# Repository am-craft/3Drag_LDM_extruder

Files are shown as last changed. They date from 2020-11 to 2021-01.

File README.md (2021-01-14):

# 3Drag LDM extruder

This repository contain all the 3D model designed for the 3Drag 3D printer's extruder @ [+LAB](www.piulab.it).






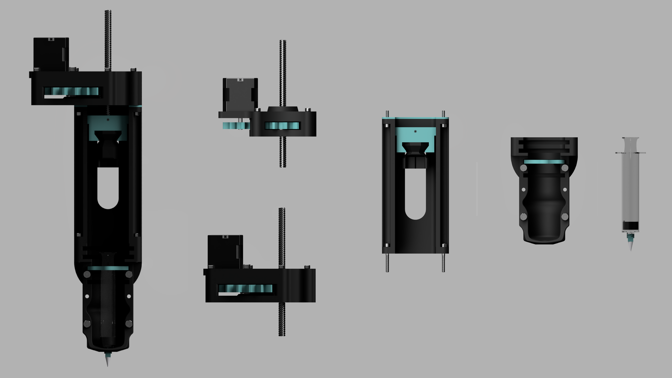
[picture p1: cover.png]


LDM (liquid Deposition Modeling) is a particular 3D printer process in which viscous fluid are extruded from a reservoir and deposited on the build plate. This process is also known as Direct Ink Writing (DIW).

The third version of the LDM extruder was developed with the porpuse of making a modular extruder, easy to assemble and disasseble.
- The syringe holder is stronger of the previour version and can be used to easily mount syringe from 10ml to 60ml.
- The extruder assembly is divided into three main parts. If one component broke you can easily switch is without disassembling all the extruder.
- The completely redesigned drive unit is stronger and smoother. The M8 screw has been substituted with a T8 lead screw. Two version are available with a 2:1 and 4:1 reduction. Higher reduction provide higher extrusion force and higher precision over the extruded material volume.
### Firmware mods needed:
- Change _DEFAULT_AXIS_STEPS_PER_UNIT_ for E motor according to the following equation: 
- Set to dummy the E0 thermistor.
- Set to 20°C the minimum temperature for preventing extrusion.

[BOM](https://github.com/am-craft/3Drag_LDM_extruder/blob/main/BOM.md)

Previous version of the extruder are available at thingiverse: [version 1](https://www.thingiverse.com/thing:482873), [version 2](https://www.thingiverse.com/thing:4635819)

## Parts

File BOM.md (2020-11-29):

# BOM

### Mount plate

* 4x nut M5

### Syringe holder:

* 4x bolt M5x50
* 4x nut M4

### Guide

* 2x square nut M3
* 2x set screw M3x10
* 1x bolt M4x10
* 4x bolt M4x16
* 4x bolt M4x30
* 2x steel rod (or tube) 4x157

### Gearbox 2:1 reduction

* 4x bolt M4x30
* 8x nut M4
* 2x trust bearing 10x24x9 [amazon](https://www.amazon.it/gp/product/B07G7YQS48/ref=ppx_yo_dt_b_asin_title_o02_s00?ie=UTF8&psc=1&tag=tv-auto-20)
* 1x T8 lead screw 8x200 [amazon](https://www.amazon.it/SIENOC-piombo-stampante-motore-passo-passo/dp/B07LDZY8RY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)
* 4x flat-head bolt M3x12
* 4x set screw M4x8
* 1x Nema 17 stepper motor

### Gearbox 4:1 reduction

* 5x bolt M4x40
* 10x nut M4
* 1x bolt M5x40
* 1x nut M5
* 2x trust bearing 10x24x9 [amazon](https://www.amazon.it/gp/product/B07G7YQS48/ref=ppx_yo_dt_b_asin_title_o02_s00?ie=UTF8&psc=1&tag=tv-auto-20)
* 2x trust bearing 8x16x5 [amazon](https://www.amazon.it/gp/product/B075F76KHN/ref=ppx_yo_dt_b_asin_title_o00_s00?ie=UTF8&psc=1)
* 1x T8 lead screw 8x200 [amazon](https://www.amazon.it/SIENOC-piombo-stampante-motore-passo-passo/dp/B07LDZY8RY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)
* 4x flat-head bolt M3x12
* 4x set screw M4x8
* 1x Nema 17 stepper motor

### Tools

* M4 tapper
* 8mm drill bit
* saw
* screwdrivers
* hex keys

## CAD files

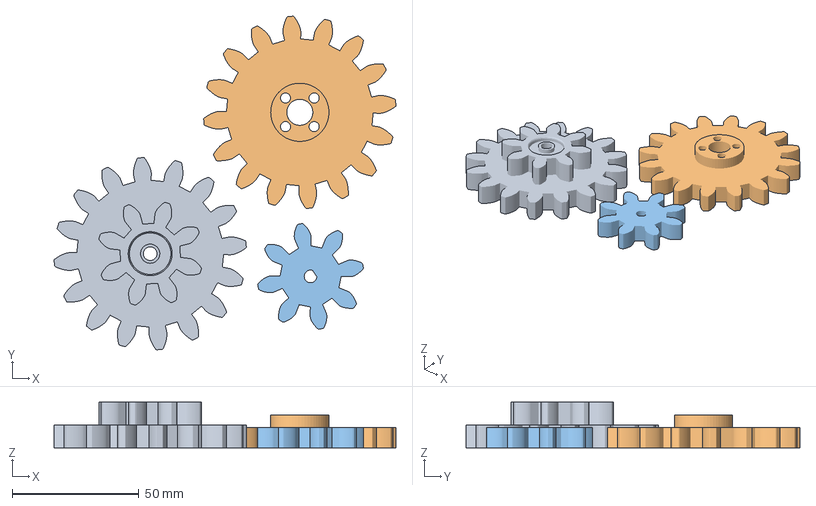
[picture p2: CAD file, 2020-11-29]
print files/4r_gears_v3.2.0.3mf
135.2 x 131.9 x 18.0 mm
4r_middle gear_v3.2.0.stl
4r_screw gear_v3.2.0.stl
motor gear_v3.0.0.stl

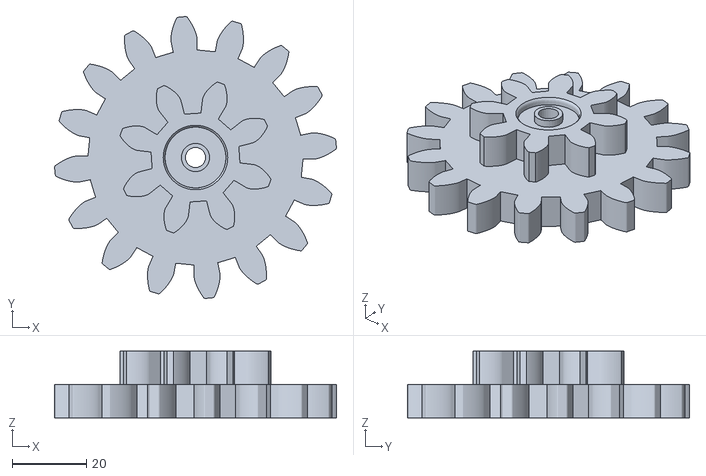
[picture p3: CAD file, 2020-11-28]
print files/STL/4r_middle gear_v3.2.0.stl
76.0 x 76.0 x 18.0

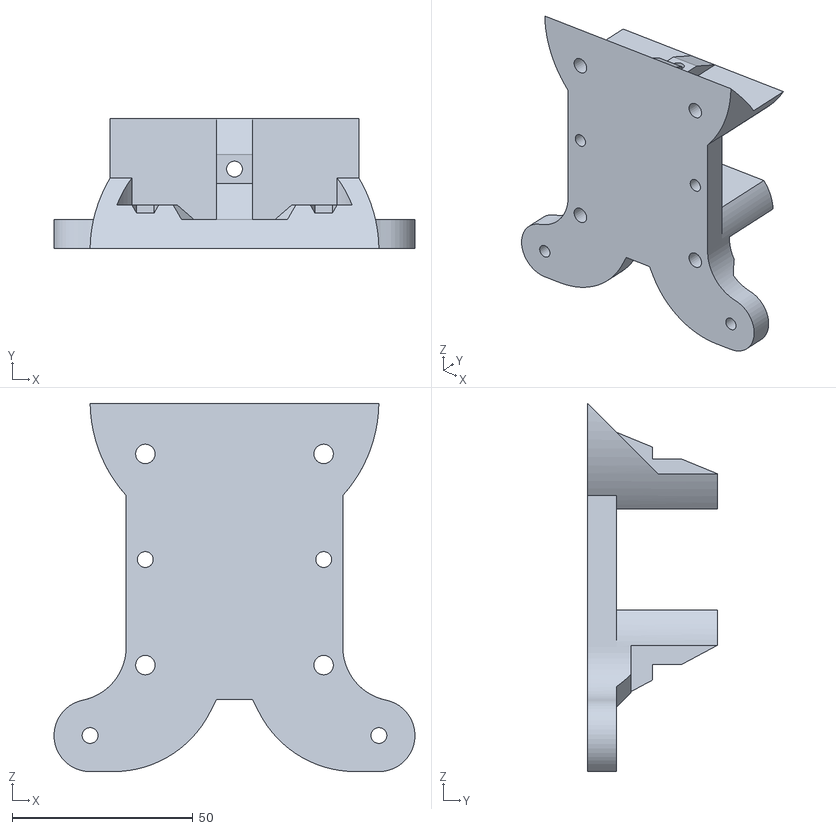
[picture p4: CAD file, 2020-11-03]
print files/STL/outDateVersion/mount plate_v3.2.0.stl
100.0 x 36.0 x 102.0

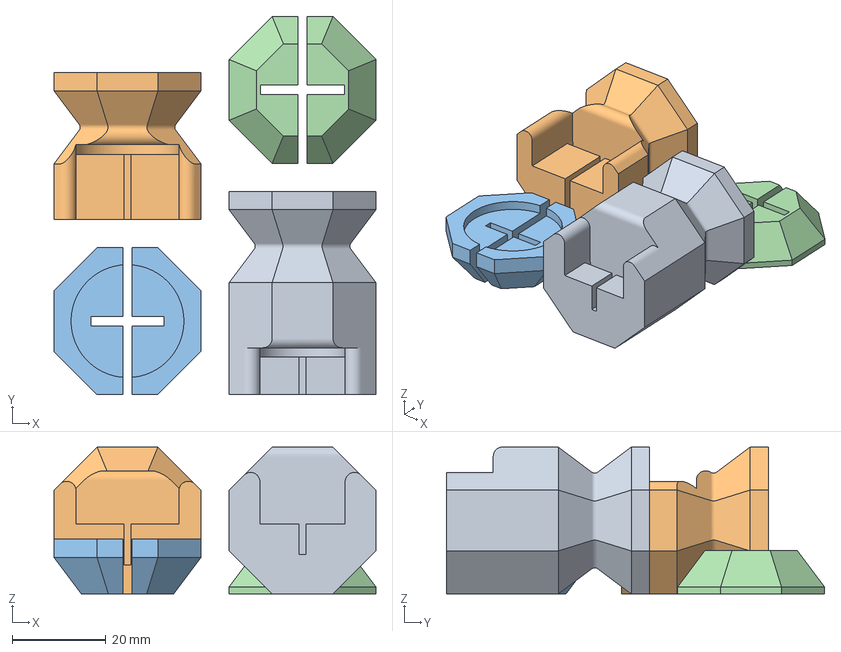
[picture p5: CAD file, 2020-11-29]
print files/piston_adapter_v3.1.0.3mf
68.8 x 80.8 x 31.4 mm
10ml piston adapter_v3.1.0.stl
20ml piston adapter_v3.1.0.stl
30ml piston adapter_v3.1.0.stl
60ml piston adapter_v3.1.0.stl

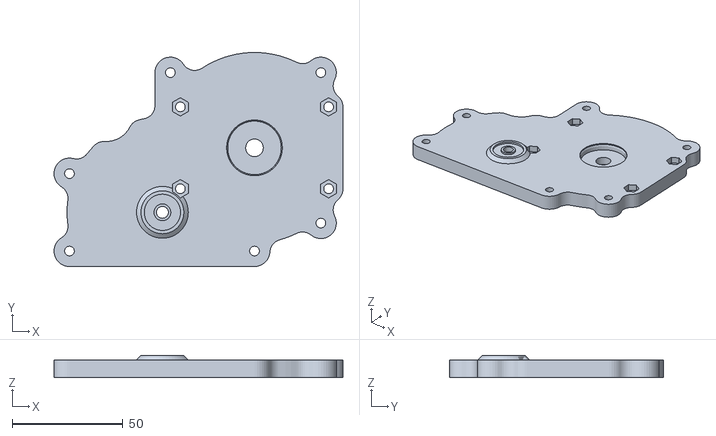
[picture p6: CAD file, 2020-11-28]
print files/STL/4r_gear box part1_v3.2.0.stl
130.6 x 96.7 x 10.0

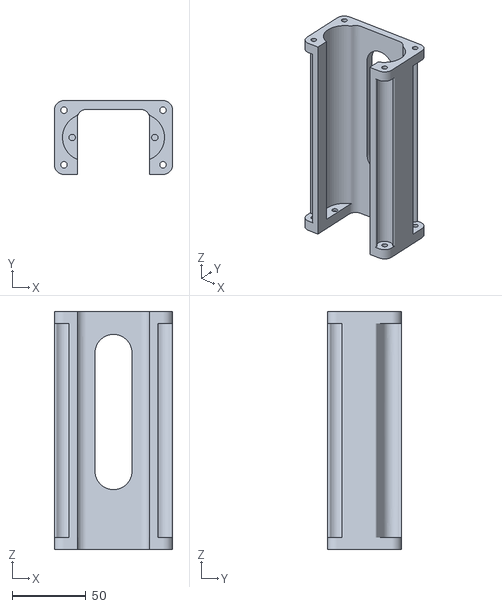
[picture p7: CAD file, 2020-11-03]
print files/STL/outDateVersion/guide_v3.1.0.stl
80.0 x 50.0 x 161.0

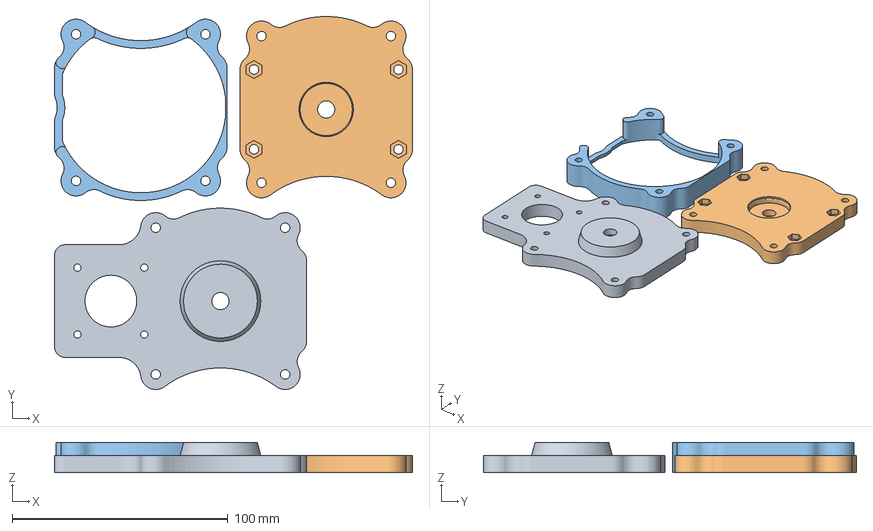
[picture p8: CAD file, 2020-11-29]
print files/2r_gear_box_v3.2.0.3mf
166.0 x 172.9 x 14.0 mm
2r_gear box part3_v3.2.0.stl
2r_gear box part1_v3.2.0.stl
2r_gear box part2_v3.2.0.stl

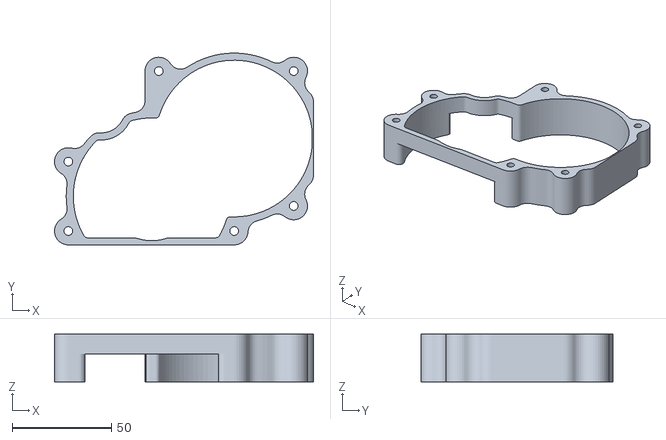
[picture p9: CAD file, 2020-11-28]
print files/STL/4r_gear box part2_v3.2.0.stl
130.6 x 96.7 x 24.0

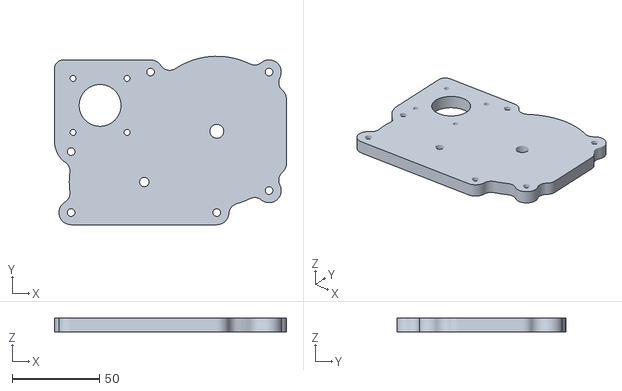
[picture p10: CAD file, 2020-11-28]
print files/STL/4r_gear box part3_v3.2.0.stl
133.2 x 96.7 x 8.00

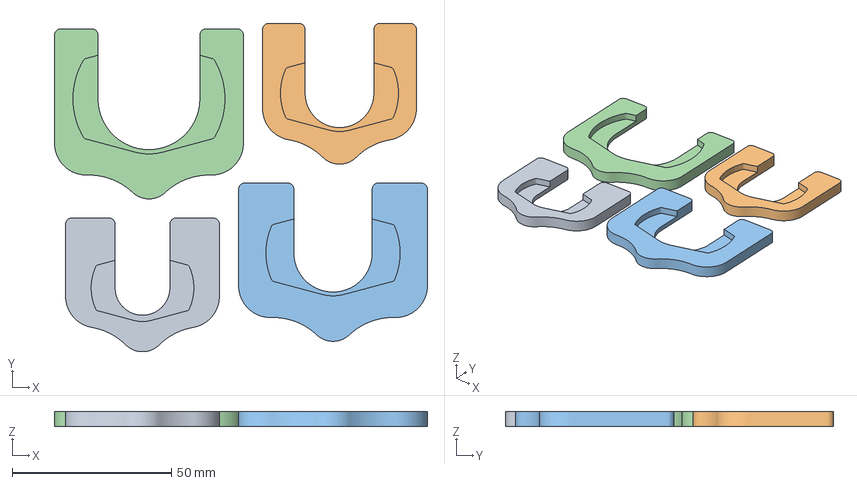
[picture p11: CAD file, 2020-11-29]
print files/syringe_adapter_v3.0.0.3mf
117.3 x 103.3 x 4.60 mm
10ml adapter_v3.0.0.stl
20ml adapter_v3.0.0.stl
30ml adapter_v3.0.0.stl
60ml adapter_v3.0.0.stl

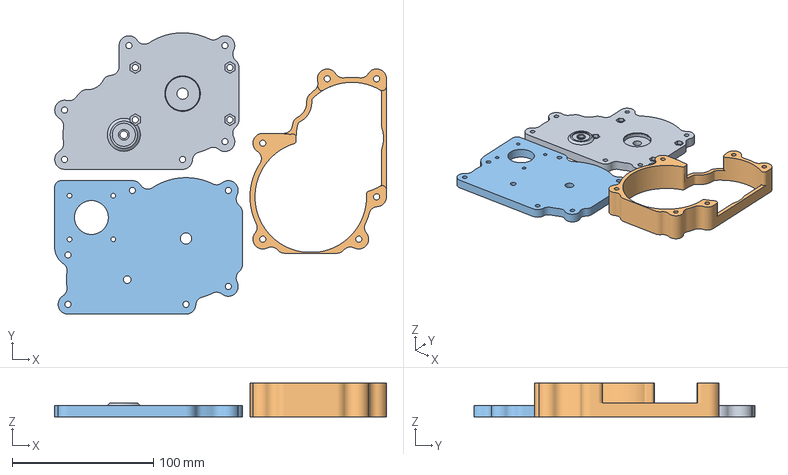
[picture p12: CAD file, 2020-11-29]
print files/4r_gear_box_v3.2.0.3mf
235.2 x 199.3 x 24.0 mm
4r_gear box part1_v3.2.0.stl
4r_gear box part2_v3.2.0.stl
4r_gear box part3_v3.2.0.stl

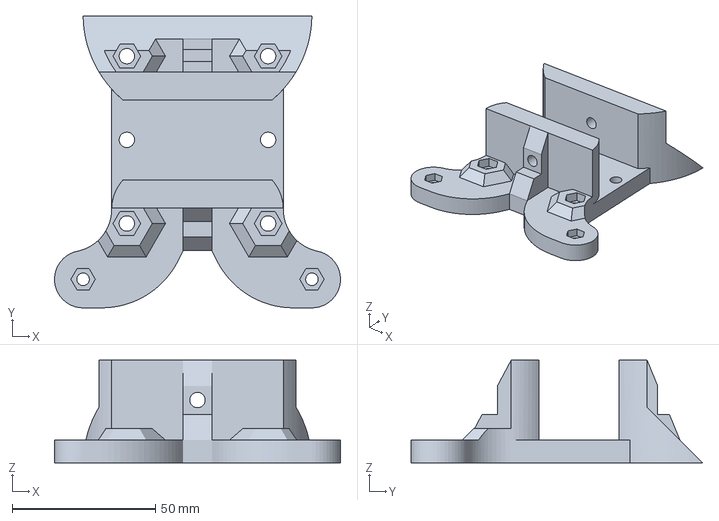
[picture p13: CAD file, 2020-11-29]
print files/mount_plate_v3.2.1.3mf
100.0 x 102.0 x 36.0 mm

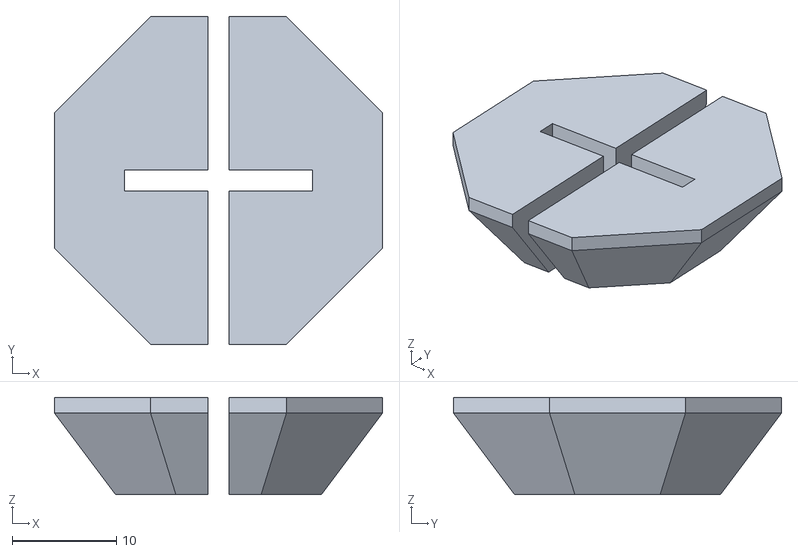
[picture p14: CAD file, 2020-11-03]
print files/STL/60ml piston adapter_v3.1.0.stl
31.4 x 31.4 x 9.30

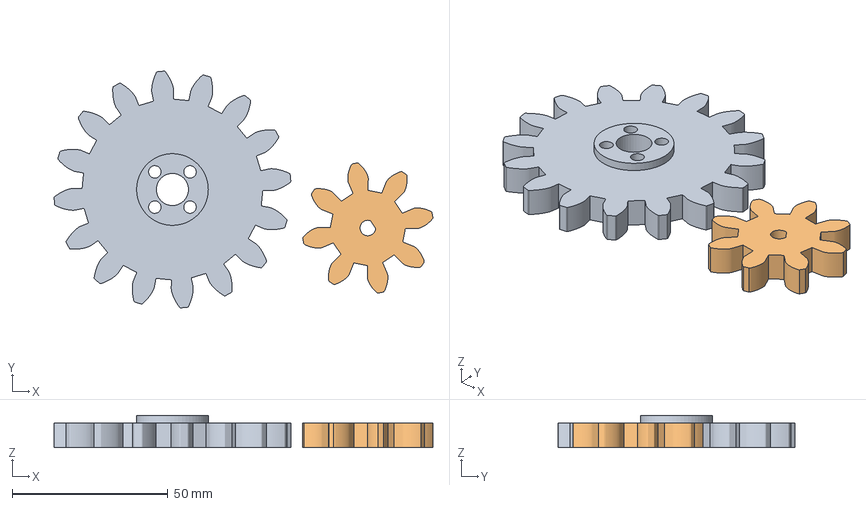
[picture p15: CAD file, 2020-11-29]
print files/2r_gears_v3.2.0.3mf
121.6 x 76.0 x 10.4 mm
2r_screw gear_v3.2.0.stl
motor gear_v3.0.0.stl

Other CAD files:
print files/STL/10ml piston adapter_v3.1.0.stl
print files/STL/30ml adapter_v3.0.0.stl
print files/syringe_holder_v3.2.0.3mf
print files/guide_v3.1.1.3mf
CAD model/3Drag mount plate v3.2.0.f3d
CAD model/3Drag mount plate v3.2.1.f3d
CAD model/Piston guide v3.2.0.f3d
CAD model/Piston guide v3.2.1.f3d
CAD model/Syringe holder v3.2.0.f3d
CAD model/outDateVersion/Piston guide v3.2.0.f3d
print files/STL/10ml adapter_v3.0.0.stl
print files/STL/20ml adapter_v3.0.0.stl
print files/STL/20ml piston adapter_v3.1.0.stl
print files/STL/2r_gear box part1_v3.2.0.stl
print files/STL/2r_gear box part2_v3.2.0.stl
print files/STL/2r_gear box part3_v3.2.0.stl
print files/STL/2r_screw gear_v3.2.0.stl
print files/STL/30ml piston adapter_v3.1.0.stl
print files/STL/4r_screw gear_v3.2.0.stl
print files/STL/60ml adapter_v3.0.0.stl
print files/STL/guide cap_v3.0.0.stl
print files/STL/guide_v3.1.1.stl
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

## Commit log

2020-11-03 uploaded 3D models
    [10ml adapter_v3.0.0.stl, 10ml piston adapter_v3.1.0.stl, 20ml adapter_v3.0.0.stl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]
2020-11-03 model fix
    [Piston guide v3.2.0.f3d, Piston guide v3.2.1.f3d, guide_v3.1.0.stl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]
2020-11-21 preparing for Zenodo submission
    [Piston guide v3.2.0.f3d, Piston guide v3.2.1.f3d, guide_v3.1.0.stl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]
2020-11-28 4r gear box
2020-11-29 prusa slicer project
    [2r_gear_box_v3.2.0.3mf, 2r_gears_v3.2.0.3mf, 4r_gear_box_v3.2.0.3mf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]
2020-11-29 STL folder
    [10ml adapter_v3.0.0.stl, 10ml piston adapter_v3.1.0.stl, 20ml adapter_v3.0.0.stl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]
